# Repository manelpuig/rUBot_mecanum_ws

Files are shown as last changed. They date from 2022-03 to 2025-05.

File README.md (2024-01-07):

# rUBot_mecanum
This rubot_mecanum workspace is organized in the following sections:
| Document | Contents |
|---|---|
| 1. rUBot Mecanum Setup  | Install and Setup rUBot_mecanum workspace|
| 2. rUBot Mecanum Bringup  | Bringup the rUBot_mecanum|
| 3. rUBot Mecanum Control  | Navigation and control|
| 4. rUBot HW Mecanum Slam&Navigation | Slam and Navigation |
| 5. rUBot  Projects | SW and HW projects |
|

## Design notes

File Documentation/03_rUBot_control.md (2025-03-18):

# **rUBot mecanum control**

The objectives of this chapter are:
- control in virtual environment 
- control with real rUBot

We have created different activities in this section:
- Robot performances
    - Keyboard control
    - Python programming control
- Autonomous control with obstacle avoidance
- Robot Wall follower
- Robot go to pose

The final model represents the real rUBot we will use in the laboratory

The rUBot mecanum robot we will work is represented in the picture:
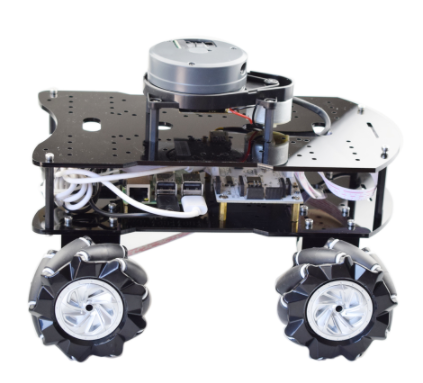
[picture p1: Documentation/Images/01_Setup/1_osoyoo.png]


**Bibliography:**
- https://bitbucket.org/theconstructcore/workspace/projects/PS

## **1. rUBot mecanum performances**

For navigation control of our robot, I have created a ROS Package "rubot_control". If you want to create it from scratch you would have to type:
```shell
cd ~/rubot_mecanum_ws/src
catkin_create_pkg rubot_control rospy std_msgs sensor_msgs geometry_msgs nav_msgs
cd ..
catkin_make
```

### **1.1. Kinematics model of mecanum robot**
The rUBot mecanum is based on a 4-wheels and has a Mecanum-drive kinematics model. We have first to analyse its kinematics model to properly control it.

Wheeled mobile robots may be classified in two major categories, holonomic (omnidirectional) and nonholonomic. 
- **Nonholonomic mobile robots**, such as conventional cars, employ conventional wheels, which prevents cars from moving directly sideways.
- **Holonomic mobile robots**, such as mecanum cars, employ omni or mecanum wheels, which allow lateral and diagonal movements

The rUBot mecanum corresponds to a Kinematic model for Holonomic Mecanum wheeled robot:

Omnidirectional wheeled mobile robots typically employ either omni wheels or mecanum wheels, which are typical wheels augmented with rollers on their outer circumference. These rollers spin freely and they allow sideways sliding while the wheel drives forward or backward without slip in that direction.

The **different movements** our car can perform are:
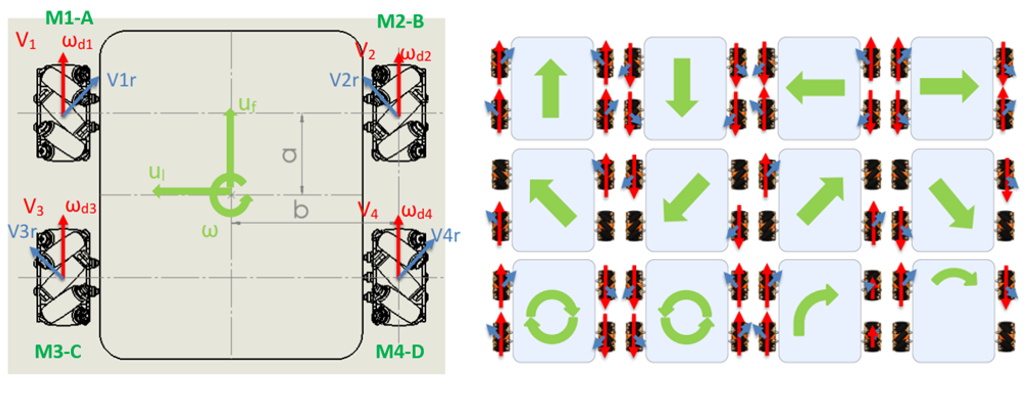
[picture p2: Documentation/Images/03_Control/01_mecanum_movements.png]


The **forces** involved define the robot linear and angular movement:
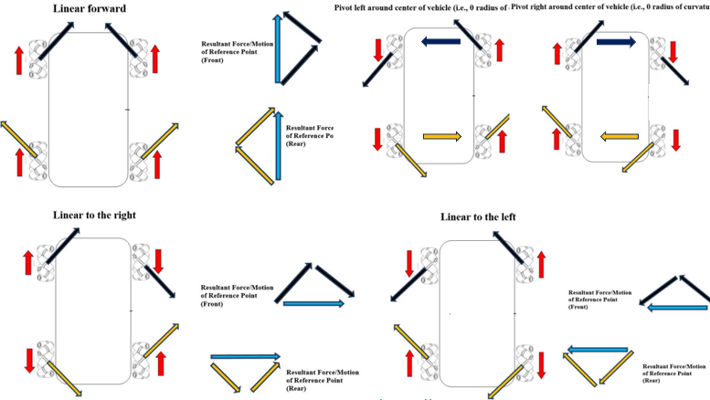
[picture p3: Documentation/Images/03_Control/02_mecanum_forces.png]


The **Forward Kinematics** equations are defined below:


where

- Vi: Linear speed of the wheels.
- ωdi: Angular speed of the wheels.
- Vir: Tangential speed of the rollers.
- ul: Linear velocity of the system on the X axis.
- uf: Linear velocity of the system on the Y axis.
- ω: Speed of rotation of the system on the Z axis.
- a: Distance from the center of the robot to the axis of rotation of the wheel.
- b: Distance from the center of the robot to the center of the width of the wheel.

>(see [Lynch & Park, 2017] for a complete derivation of this model).

In the **Inverse Kinematics** we want to apply a robot movement defined by:
- a linear and angular velocity using a Twist message type published in a /cmd_vel topic. 
- we need to calculate the 4 wheel speeds needed to obtain this robot velocity

This is defined by the following expressions:
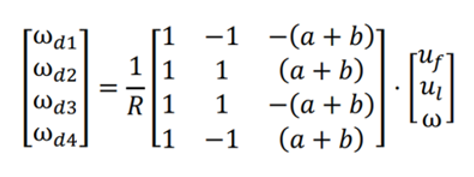
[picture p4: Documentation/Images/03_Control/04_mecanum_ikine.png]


To obtain the **Odometry** we use the information of (uf,ul,w) and Gazebo plugin calculates the POSE of our robot.

The analytical expressions are explained graphically in the picture:
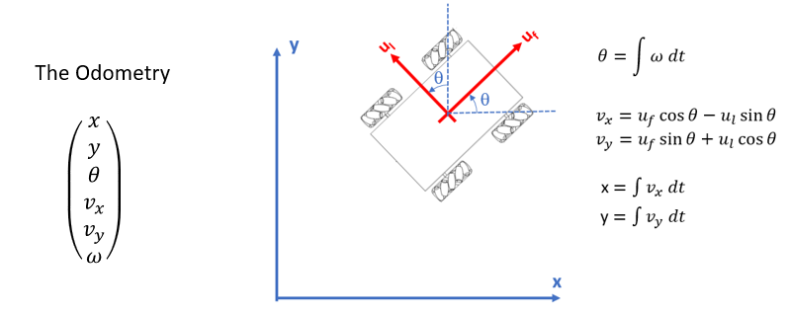
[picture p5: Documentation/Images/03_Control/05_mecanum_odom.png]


In the case of real mecanum robot this is calculated by the robot driver as an arduino program in arduino-mega platform.

### **1.2. rUBot control in VIRTUAL environment**
We can control the movement of our robot using:
- the keyboard or a joypad
- programatically in python creating a "/rubot_nav" node

We are now ready to launch control actions.

We first bringup our robot:
``` shell
roslaunch rubot_mecanum_description rubot_bringup_sw.launch
```
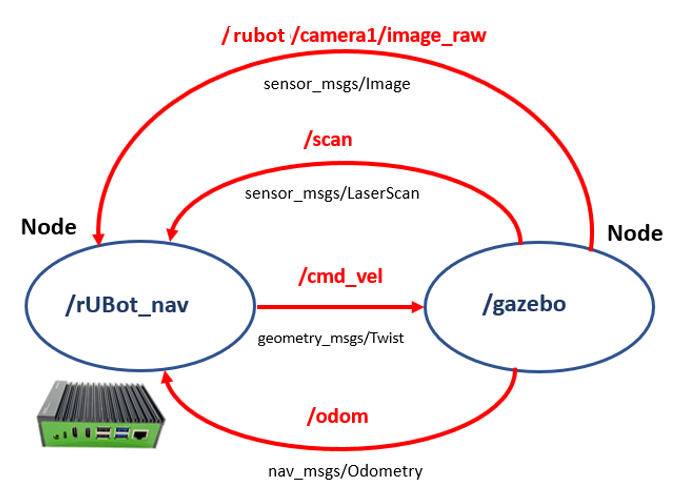
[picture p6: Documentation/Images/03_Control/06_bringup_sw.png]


#### **a) Keyboard control**
You can control the rUBot with the keyboard installing the teleop-twist-keyboard package:
```shell
sudo apt-get install ros-noetic-teleop-twist-keyboard
```

Then you will be able to control the robot with the Keyboard typing:
```shell
rosrun teleop_twist_keyboard teleop_twist_keyboard.py
```
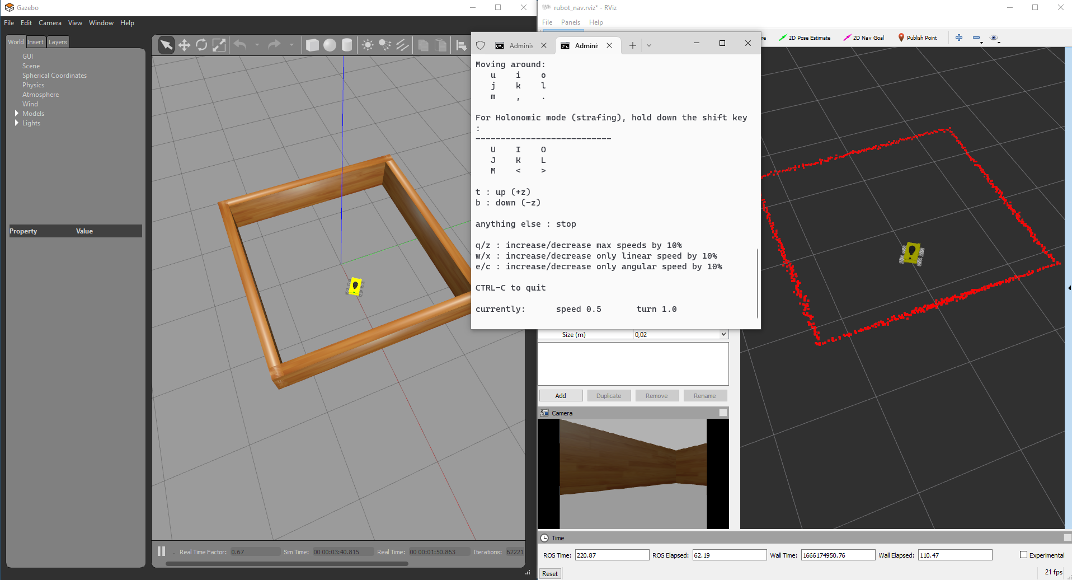
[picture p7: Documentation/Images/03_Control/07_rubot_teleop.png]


#### **b) Python programming control**

A first simple navigation program is created to move the robot according to a speciffic Twist message.

We will create now a first navigation python files in "src" folder:
- rubot_control.py: to define a rubot movement with linear and angular speed during a time td

Specific launch file have been created to launch the node and python file created above:
```shell
roslaunch rubot_control rubot_control.launch
```
Verify first that the code is working in the simulated environment.

**Activity: rUBot control in a predefined Trajectory**

If the robot moves in the correct direction, you can follow with the next objective: Create a new node for **path trajectory** definition:

- Write a new rubot_path_control.py python file that:
    - creates a rubot_nav node
    - includes parameters: v, w, and trajectory time
    - verify the functions: square_path() and triangular_path()
    - define your proper function (star(), rombe(), etc.)
- Write the corresponding rubot_path_control.launch file
- Verify and demonstrate the execution:
``` shell
roslaunch rubot_control rubot_path_control.launch
```

### **1.3. rUBot control in REAL environment**

In real environment, the bringup process depends on the real robot.

To bringup the rUBot_mecanum, execute in a first terminal:
``` shell
roslaunch rubot_mecanum_description rubot_bringup_hw_arduino.launch
```
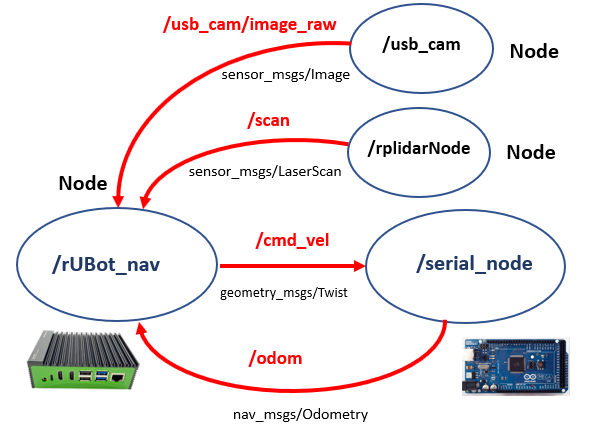
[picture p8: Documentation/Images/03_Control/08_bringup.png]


**Important!**: If you are using the RRL service from TheConstruct, the bringup is already done on boot! You have only to connect to the Real Robot.

#### **a) Keyboard control**
You can control the rUBot with the keyboard if you have first connected to the real robot within RRL service.

#### **b) Joy control**

You can control the rUBot with the Joypad following the instructions in: 
https://dev.to/admantium/radu-control-the-robot-using-a-joystick-976

- 
- In order to work with any gamepad, we need to install additional ROS packages:
```shell
sudo apt-get install ros-noetic-teleop-twist-joy ros-noetic-joy
```
- These packages provide several ways to interact with a connected joypad. To get started, we will run a ROS node called joy_node with the parameter of the detected device file.
```shell
rosrun joy joy_node dev:=/dev/input/js0
```
- to translate the messages from the /joy topic to TWIST messages, another ROS package already performs this translation. We just need to start the teleop_twist_joynode:
```shell
rosrun teleop_twist_joy teleop_node 
```
- connect the gamepad and select the Mode2 (green and red leds)
- Subscribe to the topic /cmd_vel. Then, on your gamepad, identify the deadman switch button (in our gamepad is the triangle button) and you should see messages published on /cmd_vel topic.
- You can see that this enable a non-holonomic movement
- To enable the **holonomic movement**, you have to configure the proper parameters. 
- An exemple is created to start the 2 nodes with the proper configuration parameters. This is the **rubot_joy.launch** file.

```shell
roslaunch rubot_control rubot_joy.launch
```
> For button mapping documentation refer to: http://wiki.ros.org/joy or http://wiki.ros.org/ps3joy
> for detailed configuration of launch file refer to: https://github.com/ros-teleop/teleop_twist_joy/blob/indigo-devel/launch/teleop.launch

Cool! If you have made the bringup of your robot, you will automatically feed these messages to your robot, and you can start moving around, controlled with a gamepad.

#### **c) Smart-Phone control**
ROS-Mobile is an Android application designed for dynamic control and visualization of mobile robotic system operated by the Robot Operating System (ROS). The application uses ROS nodes initializing publisher and subscriber with standard ROS messages. (https://github.com/ROS-Mobile/ROS-Mobile-Android)

- Download from Google Playstore:
Simply go to the Google Playstore Website of the ROS-Mobile app and download it. It will be installed automatically. This video shows the installation and operation process: https://www.youtube.com/watch?v=T0HrEcO-0x0
- Connect via ssh to the Master located in the RaspberryPi4 onboard computer
- Create a proper Dashboard with the joypad desried configuration

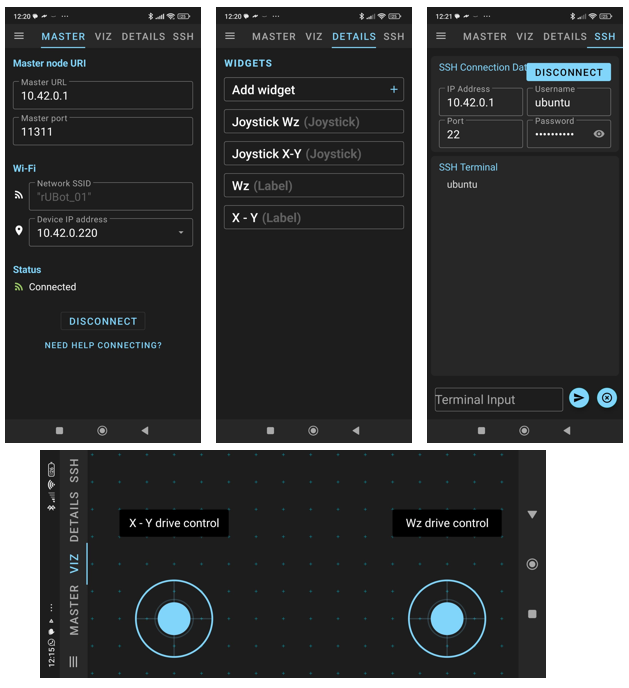
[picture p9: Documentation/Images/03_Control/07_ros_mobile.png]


> Every change you make you have to disconnect and connect again to proper operation

#### **d) Python programming control**
In the previous session we have created a python node to publish a Twist message in /cmd_vel topic. Verify the previous rubot_nav.launch file created for this purpose:
``` shell
roslaunch rubot_control rubot_control.launch
```
**Lab session: rUBot navigation in a predefined Trajectory**

If the robot moves in the correct direction, you can follow with the next objective: Create a new node for **path trajectory** definition:

- Write a new rubot_path_nav.py python file that:
    - creates a rubot_nav node
    - includes parameters: v, w, and trajectory time
    - verify the functions: square_path() and triangular_path()
    - define your proper function (star(), rombe(), etc.
- Write the corresponding rubot_path_nav.launch file
- Verify and demonstrate the execution:
``` shell
roslaunch rubot_control rubot_path_control.launch
```
Verify different trajectories inside your world
Upload the:

- rubot_path_control.launch and rubot_path_control.py files
- Video of the execution in REAL environment

## **2. Autonomous navigation with obstacle avoidance**
We will use now the created world to test the autonomous navigation with obstacle avoidance performance. 

An interesting program is described in: https://www.youtube.com/watch?v=qO7Y1PCkB8g&t=624s

The algorithm description functionality, created in "rubot_self_control.py" file,is:
- The created node makes the robot go forward.
    - LIDAR is allways searching the closest distance and the angle
    - when this distance is lower than a threshold, the robot goes backward with angular speed in the oposite direction of the minimum distance angle.

Let's verify first this behaviour in virtual environment

### **2.1. Self-control in VIRTUAL environment**

We have to launch the "rubot_self_control.launch" file in the "rubot_control" package.
```shell
roslaunch rubot_mecanum_description rubot_bringup_sw.launch
roslaunch rubot_control rubot_self_control.launch
```

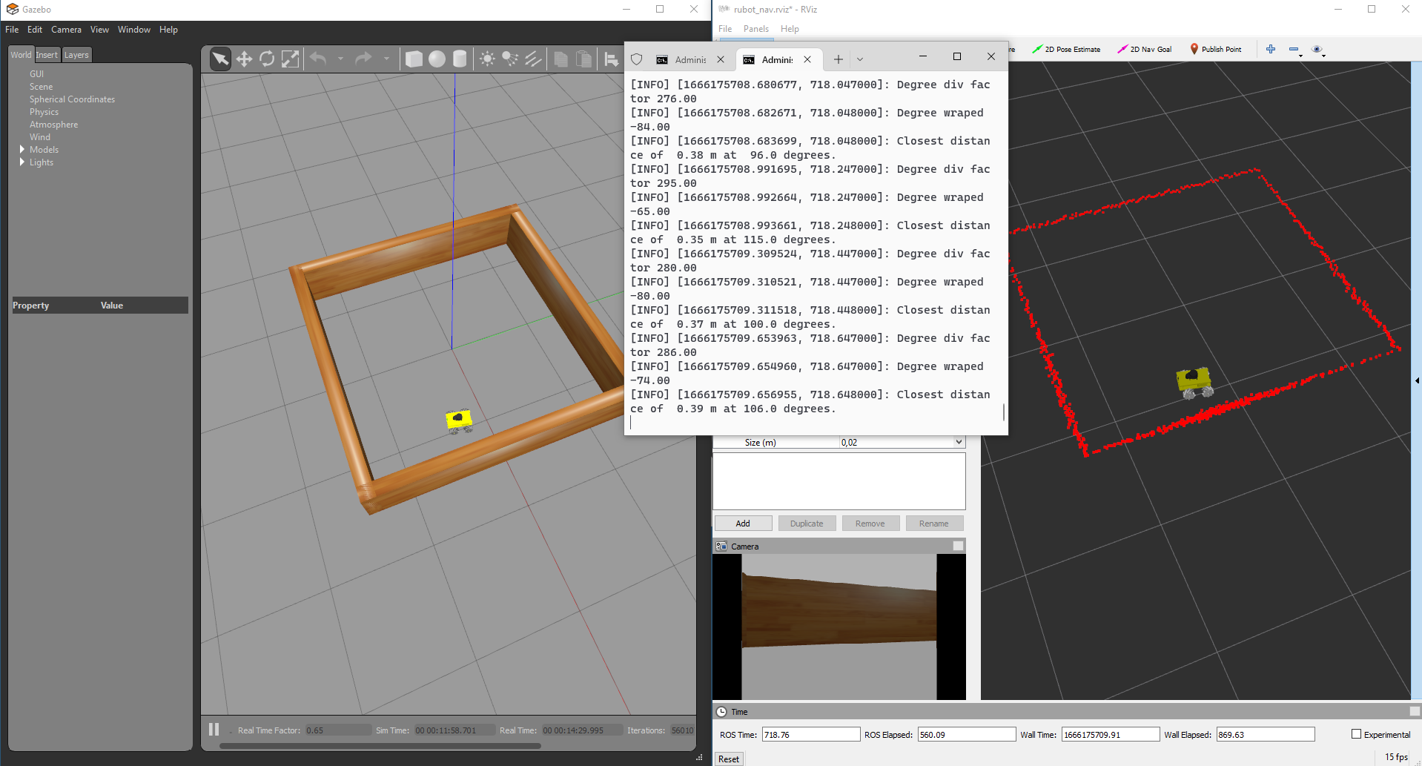
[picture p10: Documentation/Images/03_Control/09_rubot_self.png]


>- Verify in rviz if you have to change the fixed frame to "odom" frame
>- You can test the behaviour when tunning the parameters defined

**Activity: rUBot self-control**

The objective of this activity is to modify the code to move the robot in Holonomic way, for exemple:
-  When the minimum distance is in the right side move the robot over the left side

Design the code using the Holonomic robot performances, and upload:
- the file "rubot_self_control_holonomic.py"
- a video of the current behaviour in your designed world

### **2.2. Self-control control in REAL environment**

Connect first to the Real robot within RRL service.

Then verify the obstacle avoidance behaviour for different parameter values.
```shell
roslaunch rubot_control rubot_self_control.launch
```
The robot is not working as expected because the number of laser beams is not 720 as in simulation!

**Lab Activity: rUBot self-control**

The objective of this lab session is:
- take into account the number of laser beams of your Lidar in the python code
- verify the designed holonomic self-control node you have created for virtual environment in the previous activity.

Upload the:
- rubot_self_control_holonomic.launch and rubot_self_control_holonomic.py files
- Video of the execution in REAL environment

## **3. Wall Follower**
Follow the wall accuratelly is an interesting challenge to make a map with precision to apply SLAM techniques for navigation purposes.

There are 2 main tasks:
- Create a python file "rubot_wall_follower.py" to perform the wall follower in the maze of our mecanum robot
- Create a launch file "rubot_wall_follower.launch" to initialyse all the needed nodes in our system for this control task

### **3.1. Wall follower in VIRTUAL environment**

We have created a rubot_wall_follower_rg.py file based on the reading distances from LIDAR in the ranges: front, front-right, right and back-right, and perform a specific actuation in function of the minimum distance readings.

Follow the instructions to create the rubot_wall_follower_rg.py python file: https://www.theconstructsim.com/wall-follower-algorithm/

The algorith is based on laser ranges test and depends on the LIDAR type:
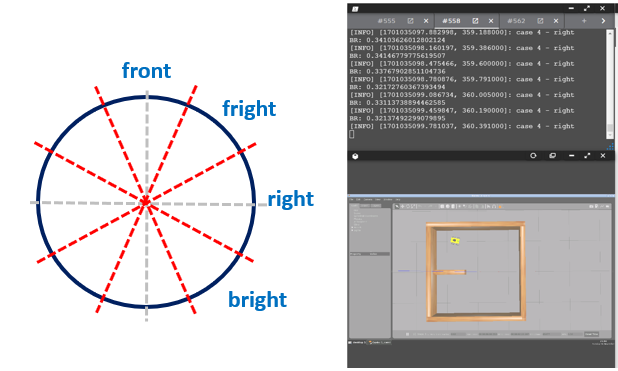
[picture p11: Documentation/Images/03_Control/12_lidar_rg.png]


Open a terminal and type:
```shell
roslaunch rubot_mecanum_description rubot_bringup_sw.launch
roslaunch rubot_control rubot_wall_follower_rg.launch
```
The wall-follower algorithm is not finished and surelly your robot is not able to follow the wall!

**Activity: rUBot wall-follower**

The objective of this activity is:
- Understand the wall-follower algorithm
- complete the code to follow the walls of your designed world
- verify the performances with a concave corners
- create a new algorithm using the holonomic performances of rUBot mecanum

Upload:
- the rubot_wall_follower.py code completed
- video of simulated behaviour in concave corners
- the proposed code "rubot_wall_follower_holonomic.py"
- video of simulated behaviour with holonomic performances

### **3.2. Wall follower in REAL environment**

Connect first to the Real robot within RRL service.

Then verify the obstacle avoidance behaviour for different created programs.

```shell
roslaunch rubot_control rubot_wall_follower_rg.launch
```
**Lab Activity 5: rUBot wall-follower HW**

The objective of this activity is:
- verify the performances of the designed code in the previous activity with your real rUBot
- Improve your new algorithm using the holonomic performances of rUBot mecanum

Upload:
- video of simulated behaviour in concave corners
- the proposed code "rubot_wall_follower_holonomic.py"

## **4. Go to POSE**
Define a specific Position and Orientation as a target point to go:
- x target point
- y target point
- f yaw orientation angle in deg

### **4.1. Go to POSE in VIRTUAL environment**

A node is created in "rubot_go2pose.py" file to reach the POSE destination with a tolerance. We have modified the python script developed in turlesim control package according to the odom message type

For validation type:
```shell
roslaunch rubot_mecanum_description rubot_bringup_sw.launch
roslaunch rubot_control rubot_go2pose.launch
```
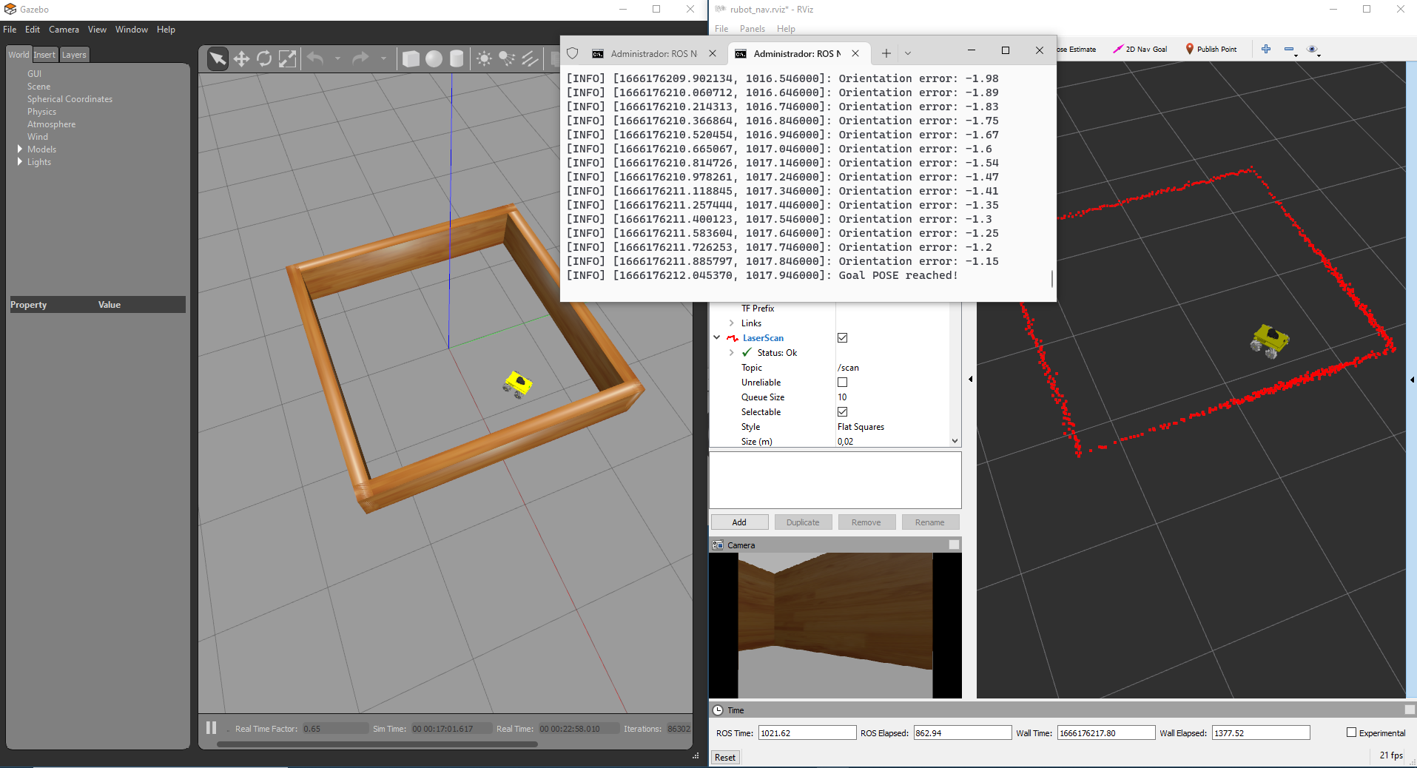
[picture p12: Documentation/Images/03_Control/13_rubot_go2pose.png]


Test different POSE targets before to test it with REAL robot.

### **4.2. Go to POSE in REAL environment**

In a real environment, there is very important the POSE precision. The Odometry computing is made with wheels readings. The floor characteristics and slings can produce inacuracies in odometry calculations.

It is important the include other sensors to obtain a better accuracy. In our case we have included an IMU sensor to obtain a better measurement of the orientation.

We will test the obtained POSE accuracy computing the Odometry with the wheel readigns

Connect first to the Real robot within RRL service.

- Then verify the same node with the real Mecanum robot:
```shell
roslaunch rubot_mecanum_description rubot_go2pose.launch
```

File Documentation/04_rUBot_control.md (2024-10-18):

# **rUBot mecanum control**

The objectives of this chapter are:
- control in virtual environment 
- control with real rUBot

We have created different activities in this section:
- Robot performances
    - Keyboard control
    - Python programming control
- Autonomous control with obstacle avoidance
- Robot Wall follower
- Robot go to pose

The final model represents the real rUBot we will use in the laboratory

The rUBot mecanum robot we will work is represented in the picture:


**Bibliography:**
- https://bitbucket.org/theconstructcore/workspace/projects/PS

## **1. rUBot mecanum performances**

For navigation control of our robot, I have created a ROS Package "rubot_control". If you want to create it from scratch you would have to type:
```shell
cd ~/rubot_mecanum_ws/src
catkin_create_pkg rubot_control rospy std_msgs sensor_msgs geometry_msgs nav_msgs
cd ..
catkin_make
```

### **1.1. Kinematics model of mecanum robot**
The rUBot mecanum is based on a 4-wheels and has a Mecanum-drive kinematics model. We have first to analyse its kinematics model to properly control it.

Wheeled mobile robots may be classified in two major categories, holonomic (omnidirectional) and nonholonomic. 
- **Nonholonomic mobile robots**, such as conventional cars, employ conventional wheels, which prevents cars from moving directly sideways.
- **Holonomic mobile robots**, such as mecanum cars, employ omni or mecanum wheels, which allow lateral and diagonal movements

The rUBot mecanum corresponds to a Kinematic model for Holonomic Mecanum wheeled robot:

Omnidirectional wheeled mobile robots typically employ either omni wheels or mecanum wheels, which are typical wheels augmented with rollers on their outer circumference. These rollers spin freely and they allow sideways sliding while the wheel drives forward or backward without slip in that direction.

The **different movements** our car can perform are:


The **forces** involved define the robot linear and angular movement:


The **Forward Kinematics** equations are defined below:


where

- Vi: Linear speed of the wheels.
- ωdi: Angular speed of the wheels.
- Vir: Tangential speed of the rollers.
- ul: Linear velocity of the system on the X axis.
- uf: Linear velocity of the system on the Y axis.
- ω: Speed of rotation of the system on the Z axis.
- a: Distance from the center of the robot to the axis of rotation of the wheel.
- b: Distance from the center of the robot to the center of the width of the wheel.

>(see [Lynch & Park, 2017] for a complete derivation of this model).

In the **Inverse Kinematics** we want to apply a robot movement defined by:
- a linear and angular velocity using a Twist message type published in a /cmd_vel topic. 
- we need to calculate the 4 wheel speeds needed to obtain this robot velocity

This is defined by the following expressions:


To obtain the **Odometry** we use the information of (uf,ul,w) and Gazebo plugin calculates the POSE of our robot.

The analytical expressions are explained graphically in the picture:


In the case of real mecanum robot this is calculated by the robot driver as an arduino program in arduino-mega platform.

### **1.2. rUBot control in VIRTUAL environment**
We can control the movement of our robot using:
- the keyboard or a joypad
- programatically in python creating a "/rubot_nav" node

We are now ready to launch control actions.

We first bringup our robot:
``` shell
roslaunch rubot_mecanum_description rubot_bringup_sw_custom.launch
```


#### **a) Keyboard control**
You can control the rUBot with the keyboard installing the following packages:
```shell
sudo apt-get install ros-noetic-teleop-tools
sudo apt-get install ros-noetic-teleop-twist-keyboard
```

Then you will be able to control the robot with the Keyboard typing:
```shell
rosrun key_teleop key_teleop.py /key_vel:=/cmd_vel
or
rosrun teleop_twist_keyboard teleop_twist_keyboard.py
```


#### **b) Python programming control**

A first simple navigation program is created to move the robot according to a speciffic Twist message.

We will create now a first navigation python files in "src" folder:
- rubot_control.py: to define a rubot movement with linear and angular speed during a time td

Specific launch file have been created to launch the node and python file created above:
```shell
roslaunch rubot_control rubot_control.launch
```
Verify first that the code is working in the simulated environment.

**Activity 4: rUBot control in a predefined Trajectory**

If the robot moves in the correct direction, you can follow with the next objective: Create a new node for **path trajectory** definition:

- Write a new rubot_path_control.py python file that:
    - creates a rubot_nav node
    - includes parameters: v, w, and trajectory time
    - verify the functions: square_path() and triangular_path()
    - define your proper function (star(), rombe(), etc.)
- Write the corresponding rubot_path_control.launch file
- Verify and demonstrate the execution:
``` shell
roslaunch rubot_control rubot_path_control.launch
```

### **1.3. rUBot control in REAL environment**

In real environment, the bringup process depends on the real robot.

To bringup the rUBot_mecanum, execute in a first terminal:
``` shell
roslaunch rubot_mecanum_description rubot_bringup_hw_arduino.launch
```


#### **a) Keyboard control**
You can control the rUBot with the keyboard installing the following packages:
```shell
sudo apt-get install ros-noetic-teleop-tools
sudo apt-get install ros-noetic-teleop-twist-keyboard
```

Then you will be able to control the robot with the Keyboard typing:
```shell
rosrun key_teleop key_teleop.py /key_vel:=/cmd_vel
or
rosrun teleop_twist_keyboard teleop_twist_keyboard.py
```

#### **b) Joy control**
You can control the rUBot with the Joypad following the instructions in: 
https://dev.to/admantium/radu-control-the-robot-using-a-joystick-976

- In order to work with any gamepad, we need to install additional ROS packages:
```shell
sudo apt-get install ros-noetic-teleop-twist-joy ros-noetic-joy
```
- These packages provide several ways to interact with a connected joypad. To get started, we will run a ROS node called joy_node with the parameter of the detected device file.
```shell
rosrun joy joy_node dev:=/dev/input/js0
```
- to translate the messages from the /joy topic to TWIST messages, another ROS package already performs this translation. We just need to start the teleop_twist_joynode:
```shell
rosrun teleop_twist_joy teleop_node 
```
- connect the gamepad and select the Mode2 (green and red leds)
- Subscribe to the topic /cmd_vel. Then, on your gamepad, identify the deadman switch button (in our gamepad is the triangle button) and you should see messages published on /cmd_vel topic.
- You can see that this enable a non-holonomic movement
- To enable the **holonomic movement**, you have to configure the proper parameters. 
- An exemple is created to start the 2 nodes with the proper configuration parameters. This is the **rubot_joy.launch** file.

```shell
roslaunch rubot_control rubot_joy.launch
```
> For button mapping documentation refer to: http://wiki.ros.org/joy or http://wiki.ros.org/ps3joy
> for detailed configuration of launch file refer to: https://github.com/ros-teleop/teleop_twist_joy/blob/indigo-devel/launch/teleop.launch

Cool! If you have made the bringup of your robot, you will automatically feed these messages to your robot, and you can start moving around, controlled with a gamepad.

#### **c) Smart-Phone control**
ROS-Mobile is an Android application designed for dynamic control and visualization of mobile robotic system operated by the Robot Operating System (ROS). The application uses ROS nodes initializing publisher and subscriber with standard ROS messages. (https://github.com/ROS-Mobile/ROS-Mobile-Android)

- Download from Google Playstore:
Simply go to the Google Playstore Website of the ROS-Mobile app and download it. It will be installed automatically. This video shows the installation and operation process: https://www.youtube.com/watch?v=T0HrEcO-0x0
- Connect via ssh to the Master located in the RaspberryPi4 onboard computer
- Create a proper Dashboard with the joypad desried configuration



> Every change you make you have to disconnect and connect again to proper operation

#### **d) Python programming control**
In the previous session we have created a python node to publish a Twist message in /cmd_vel topic. Verify the previous rubot_nav.launch file created for this purpose:
``` shell
roslaunch rubot_control rubot_control.launch
```
**Lab Activity 3: rUBot navigation in a predefined Trajectory**

If the robot moves in the correct direction, you can follow with the next objective: Create a new node for **path trajectory** definition:

- Write a new rubot_path_nav.py python file that:
    - creates a rubot_nav node
    - includes parameters: v, w, and trajectory time
    - verify the functions: square_path() and triangular_path()
    - define your proper function (star(), rombe(), etc.
- Write the corresponding rubot_path_nav.launch file
- Verify and demonstrate the execution:
``` shell
roslaunch rubot_control rubot_path_control.launch
```
Verify different trajectories inside your world
Upload the:

- rubot_path_control.launch and rubot_path_control.py files
- Video of the execution in REAL environment

## **2. Autonomous navigation with obstacle avoidance**
We will use now the created world to test the autonomous navigation with obstacle avoidance performance. 

The algorithm description functionality, created in "rubot_self_control.py" file,is:
- The created node makes the robot go forward.
    - LIDAR is allways searching the closest distance and the angle
    - when this distance is lower than a threshold, the robot goes backward with angular speed in the oposite direction of the minimum distance angle.

Let's verify first this behaviour in virtual environment

### **2.1. Self-control in VIRTUAL environment**

We have to launch the "rubot_self_control.launch" file in the "rubot_control" package.
```shell
roslaunch rubot_mecanum_description rubot_bringup_sw_custom.launch
roslaunch rubot_control rubot_self_control.launch
```



>- Verify in rviz if you have to change the fixed frame to "odom" frame
>- You can test the behaviour when tunning the parameters defined

**Activity: rUBot self-control**

The objective of this activity is to modify the code to move the robot in Holonomic way, for exemple:
-  When the minimum distance is in the right side move the robot over the left side

Design the code using the Holonomic robot performances, and upload:
- the file "rubot_self_control_holonomic.py"
- a video of the current behaviour in your designed world

### **2.2. Self-control control in REAL environment**

To bringup the rUBot mecanum robot, execute:
```shell
roslaunch rubot_mecanum_description rubot_bringup_hw_arduino.launch
```
Then verify the obstacle avoidance behaviour for different parameter values.
```shell
roslaunch rubot_control rubot_self_control.launch
```
The robot is not working as expected because the number of laser beams is nor 720 as in simulation!

**Lab Activity: rUBot self-control**

The objective of this lab session is:
- take into account the number of laser beams of your Lidar in the python code
- verify the designed holonomic self-control node you have created for virtual environment in the previous activity.

Upload the:
- rubot_self_control_holonomic.launch and rubot_self_control_holonomic.py files
- Video of the execution in REAL environment

## **3. Wall Follower**
Follow the wall accuratelly is an interesting challenge to make a map with precision to apply SLAM techniques for navigation purposes.

There are 2 main tasks:
- Create a python file "rubot_wall_follower.py" to perform the wall follower in the maze of our mecanum robot
- Create a launch file "rubot_wall_follower.launch" to initialyse all the needed nodes in our system for this control task

### **3.1. Wall follower in VIRTUAL environment**

We have created a rubot_wall_follower_rg.py file based on the reading distances from LIDAR in the ranges: front, front-right, right and back-right, and perform a specific actuation in function of the minimum distance readings.

Follow the instructions to create the rubot_wall_follower_rg.py python file: https://www.theconstructsim.com/wall-follower-algorithm/

The algorith is based on laser ranges test and depends on the LIDAR type:


Open a terminal and type:
```shell
roslaunch rubot_mecanum_description rubot_bringup_sw_custom.launch
roslaunch rubot_control rubot_wall_follower_rg.launch
```
The wall-follower algorithm is not finished and surelly your robot is not able to follow the wall!

**Activity: rUBot wall-follower**

The objective of this activity is:
- Understand the wall-follower algorithm
- complete the code to follow the walls of your designed world
- verify the performances with a concave corners
- create a new algorithm using the holonomic performances of rUBot mecanum

Upload:
- the rubot_wall_follower.py code completed
- video of simulated behaviour in concave corners
- the proposed code "rubot_wall_follower_holonomic.py"
- video of simulated behaviour with holonomic performances

### **3.2. Wall follower in REAL environment**

To bringup the Mecanum robot, execute in a first terminal:
```shell
roslaunch rubot_mecanum_description rubot_bringup_hw_arduino.launch
```
Then verify the obstacle avoidance behaviour for different created programs.

```shell
roslaunch rubot_control rubot_wall_follower_rg_custom.launch
```
**Lab Activity 5: rUBot wall-follower HW**

The objective of this activity is:
- verify the performances of the designed code in the previous activity with your real rUBot
- Improve your new algorithm using the holonomic performances of rUBot mecanum

Upload:
- video of simulated behaviour in concave corners
- the proposed code "rubot_wall_follower_holonomic.py"

## **4. Go to POSE**
Define a specific Position and Orientation as a target point to go:
- x target point
- y target point
- f yaw orientation angle in deg

### **4.1. Go to POSE in VIRTUAL environment**

A node is created in "rubot_go2pose.py" file to reach the POSE destination with a tolerance. We have modified the python script developed in turlesim control package according to the odom message type

For validation type:
```shell
roslaunch rubot_mecanum_description rubot_bringup_sw_custom.launch
roslaunch rubot_control rubot_go2pose.launch
```


Test different POSE targets before to test it with REAL robot.

### **4.2. Go to POSE in REAL environment**

In a real environment, there is very important the POSE precision. The Odometry computing is made with wheels readings. The floor characteristics and slings can produce inacuracies in odometry calculations.

It is important the include other sensors to obtain a better accuracy. In our case we have included an IMU sensor to obtain a better measurement of the orientation.

We will test the obtained POSE accuracy with:
- Computing the Odometry with the wheel readigns
- Computing the Odometry with the wheel readigns but measuring the robot orientation using the IMU sensor.

We will have to:
- upload a new arduino program to read and calibrate the IMU sensor to measure the robot orientation
- Calibrate the IMU sensor only a first time with speciffic arduino program
- Bringup the Mecanum robot, using a new arduino program to measure the robot orientation with the IMU sensor:
```shell
roslaunch rubot_mecanum_description rubot_bringup_hw_arduino.launch
```
- Then verify the same node with the real Mecanum robot:
```shell
roslaunch rubot_mecanum_description rubot_go2pose.launch
```

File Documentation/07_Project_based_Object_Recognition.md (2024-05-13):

# Project based on Object recognition

We will describe the Computer Vision based method to identify the Traffic Sign

## Using the RbpyCam

```python
#!/usr/bin/env python

import rospy
from sensor_msgs.msg import Image
from cv_bridge import CvBridge, CvBridgeError
import cv2
import numpy as np
```
**Capturing an image from the camera**

We gonna create a class for encapsuling the attributes and callback function:

```python
class TakeAShot(object):

 def __init__(self):
        self.image_sub = rospy.Subscriber("/camera/rgb/image_raw", Image, self.camera_callback)
        self.bridge_object = CvBridge()
```
The callback function will recieve the Image object from the camera in a missage and then it will save the Image as a png file in your 

```python
 def camera_callback(self,data):
      try:
           # We select bgr8 because its the OpenCV encoding by default
           cv_image = self.bridge_object.imgmsg_to_cv2(data, desired_encoding="bgr8")
           cv2.imwrite("image.png", cv_image)
      except CvBridgeError as e:
           print(e)        
```     		
The main is as usual:

```python
def main():

    rospy.init_node('take_a_shot', anonymous=True)
    take_a_shot = TakeAShot()
    try:
        rospy.spin()
    except KeyboardInterrupt:
        print("Shutting down")

if __name__ == '__main__':
    main()
```

### How to send a sequence of goals to ROS NavStack

* [Sending a sequence of Goals to ROS NavStack with Python](https://hotblackrobotics.github.io/en/blog/2018/01/29/seq-goals-py/)

### Basic Tutorials for image analysis using OpenCV
* [Shape Detection Using findContourns and approxPolyDP ](https://www.pyimagesearch.com/2016/02/08/opencv-shape-detection/)
* [Arrow Interpretation using findContourns and approxPolyDP](https://programs.wiki/wiki/use-opencv-to-judge-the-arrow-direction.html)
* [Detecting lines using Canny Edges and Hough Lines](https://docs.opencv.org/3.4/d9/db0/tutorial_hough_lines.html) --> [Example code ](https://github.com/michael-pacheco/opencv-arrow-detection)
* [Color Detection using HSV space](https://www.pyimagesearch.com/2015/09/14/ball-tracking-with-opencv/)
* [HSV color picker (in opencv H value goes from 0 to 179)](https://alloyui.com/examples/color-picker/hsv.html)

### Final Exercise:
#### First scenario: Image processing

* Load the room map 
* Start the navigation stack. 
* Get the coordinates of all the traffic sign using Rviz.
* Write a Python node with the folowing behaviour:
	* Go to the first sign.
	* When the robot stops:
		* take an image. 
		* recognize the object using image processing by coulour and shape. 
		* go to next sign according the signs:
			* Left: go to next sign on the left
			* Right: go to next sign on the right
			* STOP: Shutdown node.
			* Forbidden: continues to the next sign  	 

#### Second scenario: Computer Vision

* Load the room map 
* Start the navigation stack. 
* Get the coordinates of all the traffic sign using Rviz.
* Write a Python node with the folowing behaviour:
	* Go to the first sign.
	* When the robot stops:
		* take an image. 
        * recognize the object using TensorFlow model and do inference on each image
		* go to next sign according the signs:
			* Left: go to next sign on the left
			* Right: go to next sign on the right
			* STOP: Shutdown node.
			* Forbidden: continues to the next sign  

### How to train and use a TensorFlow model for object recognition:
* Go to https://teachablemachine.withgoogle.com/ and create an image project.
* Collect images with your mobile for each sign and upload them to the project.
* Train the model.
* Export the model as a keras .h5 model: 
* Install Keras and TensorFlow in the Robot: 
    ````python
    sudo pip install keras
    sudo pip install tensorflow
    ````
* Create a ROS node that uses the model for inference:
  
```python

from keras.models import load_model  # TensorFlow is required for Keras to work
import cv2  # Install opencv-python
import numpy as np

# Disable scientific notation for clarity
np.set_printoptions(suppress=True)

# Load the model
model = load_model("keras_Model.h5", compile=False)

# Load the labels
class_names = open("labels.txt", "r").readlines()

# CAMERA can be 0 or 1 based on default camera of your computer
camera = cv2.VideoCapture(0)

while True:
    # Grab the webcamera's image.
    ret, image = camera.read()

    # Resize the raw image into (224-height,224-width) pixels
    image = cv2.resize(image, (224, 224), interpolation=cv2.INTER_AREA)

    # Show the image in a window
    cv2.imshow("Webcam Image", image)

    # Make the image a numpy array and reshape it to the models input shape.
    image = np.asarray(image, dtype=np.float32).reshape(1, 224, 224, 3)

    # Normalize the image array
    image = (image / 127.5) - 1

    # Predicts the model
    prediction = model.predict(image)
    index = np.argmax(prediction)
    class_name = class_names[index]
    confidence_score = prediction[0][index]

    # Print prediction and confidence score
    print("Class:", class_name[2:], end="")
    print("Confidence Score:", str(np.round(confidence_score * 100))[:-2], "%")

    # Listen to the keyboard for presses.
    keyboard_input = cv2.waitKey(1)

    # 27 is the ASCII for the esc key on your keyboard.
    if keyboard_input == 27:
        break

camera.release()
cv2.destroyAllWindows()
```

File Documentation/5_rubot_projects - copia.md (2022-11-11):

# **rUBot mecanum challenging projects**

The projects proposed will be based on:
- rUBot navigation using python-based code
- Video and picture caption
- Image processing

The different projects will be:
- 1. rUBot takes photo
- 2. Go to specific point in the map
- 3. Go to specific point in the map and take a photo
- 4. Line follower

The image processing projects will be performed using:
- 2D raspicam
- 3D Inter Realsense camera

References OpenCV:
- http://wiki.ros.org/cv_bridge/Tutorials/ConvertingBetweenROSImagesAndOpenCVImagesPython
- https://docs.opencv.org/4.x/d6/d00/tutorial_py_root.html
- https://github.com/Akshay594/OpenCV/tree/master/tutorials

References InterRealSense:
- https://dev.intelrealsense.com/docs/ros-wrapper
- https://www.youtube.com/watch?v=GhHvuAoFC6I
- https://intel.github.io/robot_devkit_doc/pages/rs_slam.html

References for webcam:
- https://automaticaddison.com/working-with-ros-and-opencv-in-ros-noetic/

References:
- https://learn.turtlebot.com/
- https://learn.turtlebot.com/2015/02/04/1/
- https://learn.turtlebot.com/2015/02/04/2/
- https://learn.turtlebot.com/2015/02/04/3/
- https://github.com/markwsilliman/turtlebot
- http://wiki.ros.org/Camera%2BDynamixelRobotSample/CameraPictureServer
- https://industrial-training-master.readthedocs.io/en/melodic/_source/session5/OpenCV-in-Python.html

The first step is to create a new package "rubot_projects" with dependencies:
- rospy
- sensor_msgs
- std_msgs
- cv_bridge

```shell
catkin_create_pkg rubot_projects rospy std_msgs sensor_msgs cv_bridge
```
This package is already created and ready to use it!. You have not to create it.

We will perform some specific projects related to rUBot vision capabilities in a navigation process.

## **1. rUBot takes photo**
The objective is to program a python code to take a photo using raspicam in gopigo3 robot prototype.

Important information is taken from: https://learn.turtlebot.com/2015/02/04/3/

Follow the procedure:
- Identify the topic name where raspicam publishes the photo as a mesage of type sensor_msgs:
```shell
roslaunch nexus_slam rubot_world.launch 
rostopic list
```
- Then modify the "take_photo.py" python file with:
    - the proper topic name /rubot/camera1/image_raw
    - the proper photo filename in folder path: ./src/rubot_projects/photos/photo_sim.jpg
- run the "take_photo.py" python file to take a photo
```shell
rosrun rubot_projects take_photo.py
```
- Open the "photos" folder and you will see the photo1.jpg created

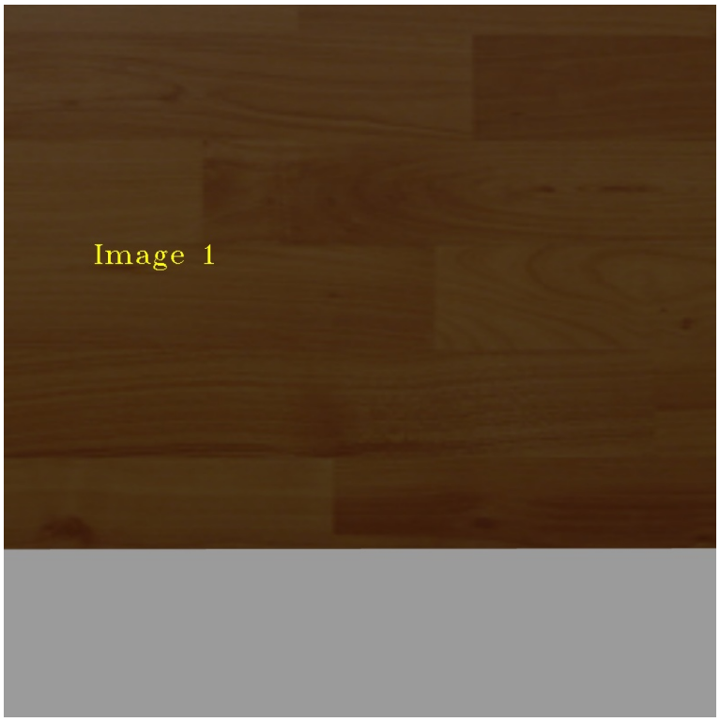
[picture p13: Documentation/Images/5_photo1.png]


## **2. Go to specific point in the map**

In this project we will learn how to send robot a command: “go to a specific position at map”.

The program is extracted from:
- https://github.com/markwsilliman/turtlebot
- https://learn.turtlebot.com/2015/02/03/11/

For this purpose we need to use the **move_base node**. This node:
- subscribes to move_base_simple/goal (geometry_msgs/PoseStamped)
- publishes to cmd_vel (geometry_msgs/Twist)



Follow the procedure:
- Launch Gazebo:
    ```shell
    roslaunch nexus_slam rubot_world.launch
    ```

- Launch the navigation:
    ```shell
    roslaunch nexus_slam rubot_navigation.launch
    ```
- Choose a target point in RVIZ using "Publish point" and select the target coordinates (i.e. x=2.0 y=-0.7)

- open "go_to_specific_point_on_map.py" and specify the target point
    - in line 78 specify the target point, customize the following values so they are appropriate for your location
        - position = {'x': 2.0, 'y' : -0.7}

- Launch the "go_to_specific_point_on_map.py" program:
    ```shell
    rosrun rubot_projects go_to_specific_point_on_map.py
    ```
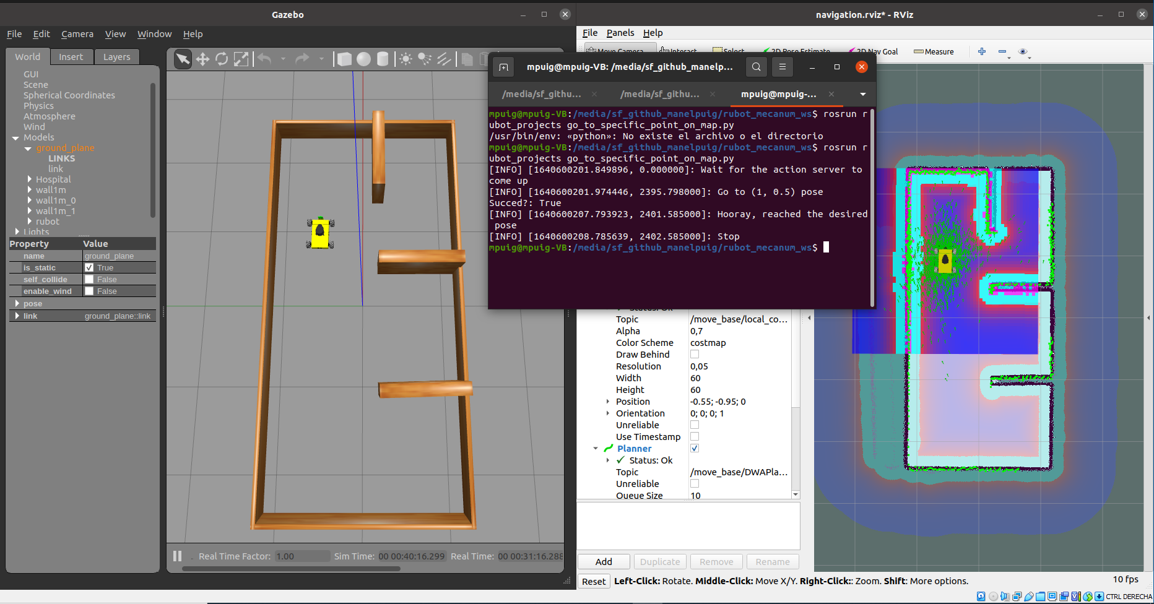
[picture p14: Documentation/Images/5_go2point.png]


## **3. Go to specific point in the map and take a photo**

We will combine our skills from two previous objectives: 
- “Going to a Specific Location on Your Map Using Code” 
- and “Taking a Photo Using Code”. 

The rUBot will go from the start to each goal from the list and take a photo in every position.

We will work with the files from: https://github.com/markwsilliman/turtlebot

Follow the instructions in: https://learn.turtlebot.com/2015/02/04/5/

We use the code go_to_specific_point_on_map.py and take_photo.py from previous exemples. 

We have generated  the python file **"Follow_the_route.py"** that reads input data from "route.yaml" file. 

The YAML file has three lines. It means that there are three goals. Look on the first line:

- {filename: 'photo1.png', position: { x: 0.355, y: -0.2}, quaternion: {r1: 0, r2: 0, r3: -0.628, r4: 0.778}}

    The dumpster.png is the image title for picture. 
    
    The position and quaternion set the goal: the place where rUBot takes a photo. 

The objective is to follow the route and take pictures. 

Proceed with the following steps:

- Launch Gazebo:
    ```shell
    roslaunch nexus_slam rubot_world.launch
    ```

- Run the navigation demo:
    ```shell
    roslaunch nexus_slam rubot_navigation.launch
    ```

- Specify a "route.yaml" file with the points to follow and take photo:

    - {filename: './src/robot_projects/rubot_projects/photos/picture1.png', position: { x: -0.3, y: -0.8}, quaternion: {r1: 0, r2: 0, r3: -0.628, r4: 0.778}}
    - {filename: './src/robot_projects/rubot_projects/photos/picture2.png', position: { x: 1.7, y: -0.7}, quaternion: {r1: 0, r2: 0, r3: 0.936, r4: 0.353}}
    - {filename: './src/robot_projects/rubot_projects/photos/picture3.png', position: { x: 1.7, y: 0.5}, quaternion: {r1: 0, r2: 0, r3: 0.904, r4: -0.427}}

- Open a terminal in the ldestination of pictures and launch the "follow_the_route.py" program:
    ```shell
    rosrun rubot_projects follow_the_route.py
    ```

>Careful!: 
Be sure to execute the rosrun instruction inside the "rubot_mecanum_ws" folder. Review the the absolute path or relative path to the yaml file and the picture path destination.

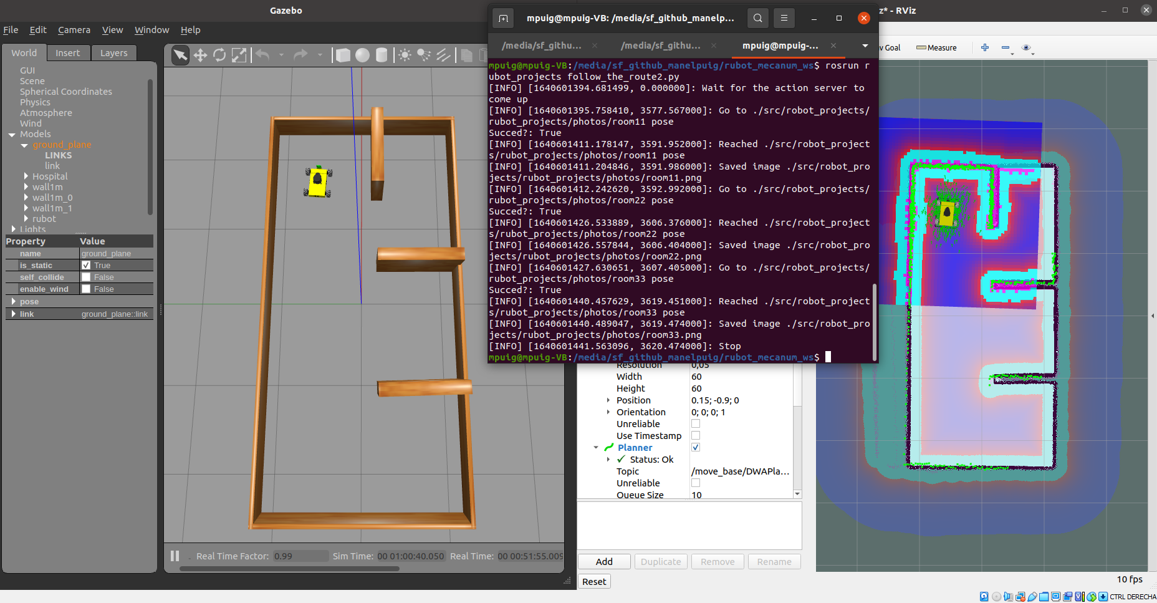
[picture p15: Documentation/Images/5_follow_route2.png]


Improvement!:
- a modified "follow_the_route2.py" and "route2.yaml" is made in order to insert the target orientation in RPY degrees
    - {filename: './src/gopigo3_projects/photos/room11.png', position: { x: -0.3, y: -0.8}, angle: {fi: -90}}
    - {filename: './src/gopigo3_projects/photos/room22.png', position: { x: 1.7, y: -0.7}, angle: {fi: 0}}
    - {filename: './src/gopigo3_projects/photos/room33.png', position: { x: 1.7, y: 0.5}, angle: {fi: 0}}

Launch the "follow_the_route.py" program:

    rosrun rubot_projects follow_the_route2.py 

## **4. Line following**
Detailed official information in: 

- https://www.theconstructsim.com/morpheus-chair-create-a-linefollower-with-rgb-camera-and-ros-episode-5/
- https://www.youtube.com/watch?v=9C7Q8bRERgM
- https://github.com/noshluk2/ROS2-Self-Driving-Car-AI-using-OpenCV

Related to the links:
- http://www.rosject.io/l/8292943/
- https://en.wikipedia.org/wiki/Differential_wheeled_robot

And with the code:
- https://bitbucket.org/theconstructcore/morpheus_chair/src/master/

The nexts steps will be:
- Define a proper simulated world in Gazebo
- spawn the robot model in Gazebo world
- setup the robot with camera
- start the line follower node

### **4.1. world setup**

We have created different models to include in gazebo world:
- Trafic signs
- lights
- road

We will construct first these models in a specific folder:
- .../rubot_mecanum_ws/src/rubot_mecanum_description/models

We have to add this folder to GAZEBO_MODEL_PATH tenvironment variable. This is done either:
-  When using ROS in UBUNTU: in ~/.bashrc file adding this line:
```xml
export GAZEBO_MODEL_PATH=$HOME/Escritorio/rUBot_mecanum_ws/src/rubot_mecanum_description/models:$GAZEBO_MODEL_PATH
```
> If you want to delete any model path from gazebo, load the "gui.ini" file from .gazebo folder. There is a list of model paths and you can delete the one you do not want
- When using ROS in WINDOWS, add in Terminal "command line":
```xml
&& set GAZEBO_MODEL_PATH=C:\Usuarios\puigm\Escritorio\ROS_github\rUBot_mecanum_ws\src\rubot_mecanum_description\models
```
- or copy the models folder in ~/.gazebo/models/
- or you have this folder already in your Gazebo Path if you have created a model using "Building Editor"

#### **a) Traffic sign**
Let's create a "sign board 30" model:
- Open Gazebo as superuser (sudo gazebo)
- select edit --> Model Editor 
- add the meshes (obj files or standard objects) needed to create the sign model
- adjust the size and place the objects in the correct positions to be assembled
- select joint in gazebo (fixed), define the parent and child links, adjust the relative pose, change the joint name if you want and create the model
- save the model as "sign_stand"
- You will see the folder created for this model with 2 files (model.config and model.sdf)
- in model.sdf you can:
  - reduce the mass of the upper links for inertial stability.
  - change the defauld color (Gazebo/Grey)
  - change the dimensions and pose of different links if necessary
- open gazebo and add the generated model to verify the size and mecanical stability.

This model will be used to create all the other traffic signs, for exemple the turn traffic sign:
- Make a copy of this folder with the name "sign_left_turn"
- in model.config file change the name to "sign_left_turn"
- add materials and meshes folders inside "sign_left_turn"
- In materials folder add scripts and textures folder
- In textures folder add the png file with the sign picture (turn.png)
- in scripts add a sign_left_turn.material file with this contents (specify the turn.png file):
```xml
material sign_left_turn/Diffuse
{
  technique
  {
    pass
    {
      texture_unit
      {
        texture turn.png
        filtering anistropic
        max_anisotropy 16
      }
    }
  }
}
```
- Open the model.sdf and change the material properties of link02 where we want to place the turn left texture. Replace the text:
```xml
        <material>
          <lighting>1</lighting>
          <script>
            <uri>file://media/materials/scripts/gazebo.material</uri>
            <name>Gazebo/White</name>
          </script>
          <shader type='pixel'/>
          <emissive>0 0 0 1</emissive>
        </material>
```
by this text:
```xml
        <material>
          <script>
            <uri>model://sign_left_turn/materials/scripts</uri>
            <uri>model://sign_left_turn/materials/textures</uri>
            <name>sign_left_turn/Diffuse</name>
          </script>
        </material>
```

- you have now the turn traffic sign ready!

#### **b) Road surface**
Let's create road surface to follow the road line:
- Open Gazebo (roslaunch gazebo_ros empty_world.launch) and in Building Editor create a model "road1" using a wall with height 5cm width 10m and length 10m. Save this model in "rUBot_mecanum_ws\src\rubot_mecanum_description\models"
- In Power point, create a picture with the road desired texture (proportional xy size is important).
- Save this picture in pgn ot jpeg format using for exemple "Recorte" from windows
- copy the png file to package folder C:/opt/ros/noetic/x64/share/gazebo-10/media/materials/textures
- open package file "C:/opt/ros/noetic/x64/share/gazebo-10/media/materials/scripts/gazebo.material"
- add this code at the end (with png file name):
```xml
material Gazebo/Road_custom
{
  technique
  {
    pass
    {
      ambient 1.0 1.0 1.0 1.0
      diffuse 1.0 1.0 1.0 1.0
      specular 0.2 0.2 0.2 1.0 12.5

      texture_unit
      {
        texture road_custom_1.png
        filtering trilinear
      }
    }
  }
}
```
- Some models and textures are in "rUBot_mecanum_ws/Documentation/Files/Model_Textures/"
- In the "road1" created model ("rUBot_mecanum_ws\src\rubot_mecanum_description\models\road1"), open "model.sdf"
- Change the material/script lines to:
```xml
<material>
  <script>
    <uri>file://media/materials/scripts/gazebo.material</uri>
    <name>Gazebo/Road_custom</name>
  </script>
```
- Open a gazebo_empty-world and create your road_custom_1.world file using the defined models

#### **c) final world**
To add models in our world add each model in the last part of your world file (here starts with empy.world):

```xml
<sdf version="1.5">
  <world name="default">
    <!-- A global light source -->
    <include>
      <uri>model://sun</uri>
    </include>
    <!-- A ground plane -->
    <include>
      <uri>model://ground_plane</uri>
    </include>
    <!-- A traffic sign -->
    <include>
      <uri>model://sign_left_turn</uri>
      <pose>0 0 0.5 0 0 0</pose>
    </include>
    <!-- Line Test 1 -->
    <include>
        <uri>model://line2</uri>
        <name>line_1</name>
        <pose>0 0 0 0 0 0</pose>
      </include> 
    <!-- Line Test 2 -->
    <include>
        <uri>model://line2</uri>
        <name>line_2</name>
        <pose>1 1.025 0 0 0 1.57</pose>
    </include> 
  </world>
</sdf>
```
Alternativelly you can open gazebo and add the desired models in proper location and save it in world format.
```shell
roslaunch gazebo_ros empty_world.launch
```

We spawn our robot into gazebo world:
```shell
roslaunch rubot_projects rubot_bringup.launch
```
To see the camera image, type:
```shell
rosrun rqt_image_view rqt_image_view
```

Start the node line_following_sim
```shell
roslaunch rubot_projects line_following.launch
```
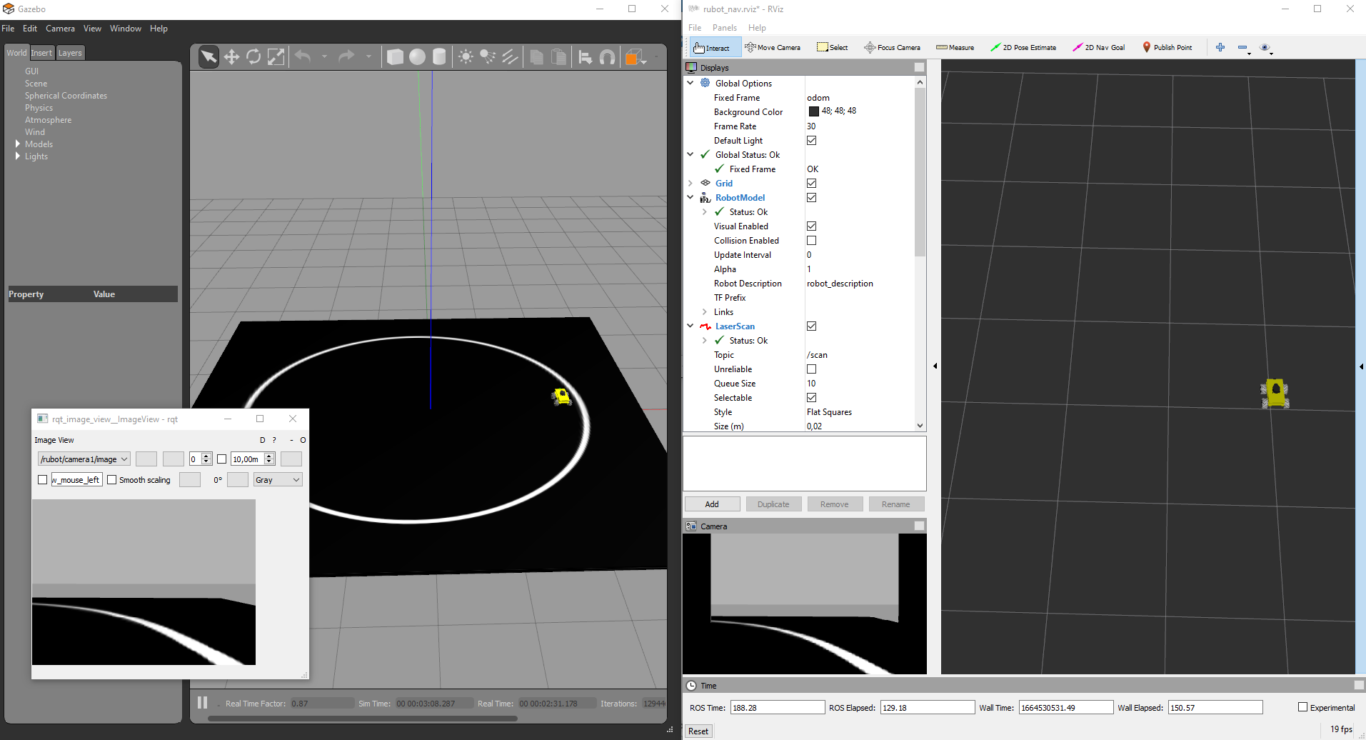
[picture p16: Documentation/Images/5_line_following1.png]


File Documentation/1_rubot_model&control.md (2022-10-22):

# **rUBot mecanum model & control**

Diferent mecanum robot prototypes are available in the market:
- Banggood: https://es.banggood.com/MC100-4WD-Wheeled-Trolley-Smart-Car-Kit-with-Mecanum-Wheel-1-48-Reduction-Ratio-TT-Motor-p-1750584.html?ID=566379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
- OSOYOO: https://www.amazon.es/dp/B082DBYH9G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
- Custom: https://howtomechatronics.com/projects/arduino-mecanum-wheels-robot/
- Nexus: https://www.robotshop.com/es/es/kit-robot-mecanum-4wd-compatible-con-arduino.html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
- Nexus2: https://www.robotshop.com/es/es/kit-robot-arduino-con-rueda-mecanum-4wd-60-mm.html
- Vikep: https://www.amazon.es/VIKEP-AutoPilot-Posicionamiento-automatizado-Conducci%C3%B3n/dp/B09MKFLFKJ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
- VIKEP_Chasis: https://www.amazon.es/VIKEP-Motores-Bricolaje-Mecanum-Plataforma/dp/B09NNFKL3Z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
- KESOTO_Chasis: https://www.amazon.es/KESOTO-Chasis-Coche-Inteligente-Mecanum/dp/B082SQ787K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

The objectives of this chapter are:
- Create a model of our rUBot 
- use rviz package to view the different topics and nodes
- create a model of the virtual environment
- use gazebo package to simulate the robot kinematics and dynamics
- locate the robot in our created environment
- create our firsts programs to control the robot movement with obstacle avoidance

The final model represents the real rUBot we will use in the laboratory

Interesting complementary information could be found:
- https://github.com/RBinsonB/nexus_4wd_mecanum_simulator

The rUBot mecanum robot we will work is represented in the picture:


His main characteristics are: 
- Arduino based control for sensors & actuators
  - Servomotor actuators for the 4 mecanum wheels
  
- RaspberryPi4 High-level onboard control with Ubuntu20 and ROS Noetic
  - RPlidar distance sensor
  - Raspicam 2D camera sensor

**Bibliography:**
- https://bitbucket.org/theconstructcore/workspace/projects/PS

## **1. rUBot mecanum model generation**

First of all, we have to create the "rubot_mecanum_description" package where we will create the rUBot model. In case you want to create it from scratch, type:
```shell
cd ~/Desktop/ROS_github/rubot_mecanum_ws/src
catkin_create_pkg rubot_mecanum_description rospy
cd ..
catkin_make
```
Then open the .bashrc file and verify the environment variables and source to the proper workspace:
```shell
source ~/Desktop/ROS_github/rubot_mecanum_ws/devel/setup.bash
```
> In ROS_windows: add && devel/setup.bat in command line of terminal configuration.

To create our robot model, we use URDF files (Unified Robot Description Format). URDF file is an XML format file for representing a robot model.(http://wiki.ros.org/urdf/Tutorials)

We have created 2 folders for model description:
- URDF: folder where different URDF models are located. In our case rubot_rp.urdf
- meshes: folder where 3D body models in stl format are located. We will have rubot folder.

You can reduce the amount of code in a URDF file using Xacro package. With this package you can use constants, simple math and macros to create your robot model easier and compact.

The main parts of URDF model are:
- links: diferent bodies/plastic elements
- joints: connection between 2 links 
- sensors & actuators plugins (2D camera, LIDAR and DC motors)

The link definition contains:
- visual properties: the origin, geometry and material
- collision properties: the origin and geomnetry
- inertial properties: the origin, mass and inertia matrix

The joint definition contains:
- joint Type (fixed, continuous)
- parent and child frames
- origin frame
- rotation axis

The geometrical definition of our rUBot is:
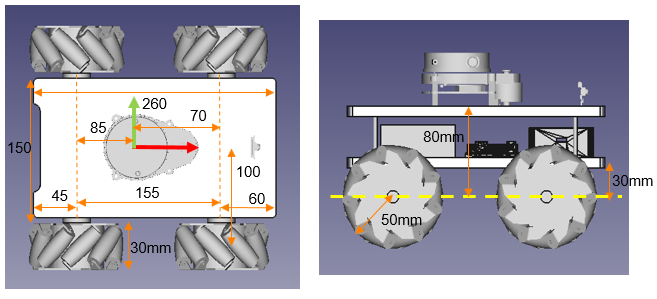
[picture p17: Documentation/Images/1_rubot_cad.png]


In the case or upper left wheel:
```xml
<!-- upper_left_wheel -->
  <joint name="upper_left_wheel_joint" type="continuous">
    <origin rpy="0 0 0" xyz="0.07 0.1 0"/>
    <parent link="base_link"/>
    <child link="upper_left_wheel"/>
    <axis xyz="0 1 0"/>
  </joint>
  <link name="upper_left_wheel">
    <visual>
      <origin rpy="0 0 0" xyz="0 0 0"/>
      <geometry>
        <mesh filename="package://rubot_mecanum_description/meshes/rubot/upper_left_wheel.stl" scale="0.001 0.001 0.001"/>
      </geometry>
      <material name="light_grey"/>
    </visual>
    <collision>
      <origin rpy="-1.57 0 0" xyz="0 0 0"/>
      <geometry>
        <cylinder length="0.03" radius="0.05"/>
      </geometry>
    </collision>
    <inertial>
      <origin rpy="-1.57 0 0" xyz="0.0 0.0 0.0"/>
      <mass value="0.1"/>
      <inertia ixx="0.00007" ixy="0" ixz="0" iyy="0.000125" iyz="0" izz="0.00007"/>
    </inertial>
  </link>
```
> Be careful with base_link:
>
> The inertia matrix can be analytically calculated with the mas and geometry. Be sure the mass is consistent and the inertia Ixx,Iyy and Izz are high enough to avoid underired drift movements. Consider the Inertia matrix you can generate using the **urdf_inertial_calculator.py** program file you have in "Documentation/files/URDF_inertial".
Possible correct values are
  ```xml
      <inertial>
        <origin rpy="0 0 0" xyz="0 0 0"/>
        <mass value="5"/>
        <inertia ixx="6" ixy="0" ixz="0" iyy="6" iyz="0" izz="12"/>
      </inertial>
  ```
The rUBot model includes different sensors and actuators:

Sensors:
- a two-dimensional camera: correspondas to RBPi camera
- a 360º RPLidar A1M8 (https://www.robotshop.com/es/es/rplidar-a1m8-kit-desarrollo-escaner-laser-360-grados.html)

Actuator:
- Mecanum drive actuator: based on 4 DC motors with encoders to obtain the Odometry information

The full model contains also information about the sensor and actuator controllers using specific Gazebo plugins (http://gazebosim.org/tutorials?tut=ros_gzplugins#Tutorial:UsingGazebopluginswithROS). 

Gazebo plugins give your URDF models greater functionality and compatible with ROS messages and service calls for sensor output and motor input. 

These plugins can be referenced through a URDF file, and to insert them in the URDF file, you have to follow the sintax:
### **Camera sensor plugin**
This sensor is integrated as a link and fixed joint for visual purposes. Review the joint and link definition in URDF model.

A driver is needed to view the images.
```xml
  <!-- 2D Camera controller -->
  <gazebo reference="camera">
    <sensor name="camera1" type="camera">
      <update_rate>30.0</update_rate>
      <camera name="front">
        <horizontal_fov>1.3962634</horizontal_fov>
        <image>
          <width>800</width>
          <height>800</height>
          <format>R8G8B8</format>
        </image>
        <clip>
          <near>0.02</near>
          <far>300</far>
        </clip>
      </camera>
      <plugin filename="libgazebo_ros_camera.so" name="camera_controller">
        <alwaysOn>true</alwaysOn>
        <visualize>true</visualize>
        <cameraName>rubot/camera1</cameraName>
        <imageTopicName>image_raw</imageTopicName>
        <cameraInfoTopicName>camera_info</cameraInfoTopicName>
        <frameName>camera</frameName>
        <hackBaseline>0.07</hackBaseline>
        <distortionK1>0.0</distortionK1>
        <distortionK2>0.0</distortionK2>
        <distortionK3>0.0</distortionK3>
        <distortionT1>0.0</distortionT1>
        <distortionT2>0.0</distortionT2>
      </plugin>
    </sensor>
  </gazebo>
  ```
>To view the camera image you can:
> - add the line in the plugin 
> ```xml
><visualize>true</visualize>"
> ```
> -  use rviz
> - type rqt in a terminal and select Plugins->Visualization->Image View
### **LIDAR sensor plugin**
This sensor is integrated as a link and fixed joint for visual purposes. Review the joint and link definition in URDF model.
> Note that rpLIDAR is mounted at 180º and you need to turn the link model and the joint to reflect this in the URDF model.

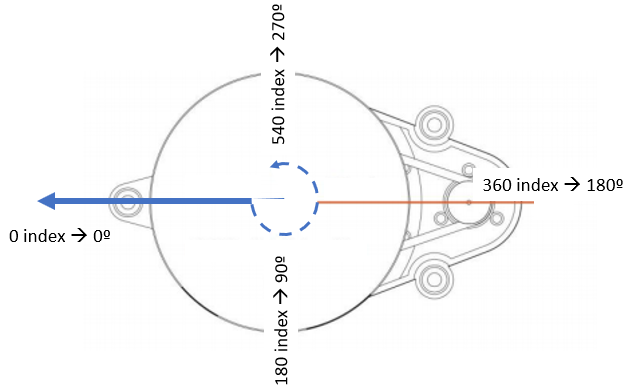
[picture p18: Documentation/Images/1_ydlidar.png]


A driver is needed to see the 720 laser distance points:
```xml
  <!-- Laser Distance Sensor YDLIDAR X4 controller-->
  <gazebo reference="base_scan">
    <sensor name="lds_lfcd_sensor" type="ray">
      <pose>0 0 0 0 0 0</pose>
      <visualize>true</visualize>
      <update_rate>5</update_rate>
      <ray>
        <scan>
          <horizontal>
            <samples>720</samples>
            <resolution>1</resolution>
            <min_angle>0.0</min_angle>
            <max_angle>6.28319</max_angle>
          </horizontal>
        </scan>
        <range>
          <min>0.12</min>
          <max>10</max>
          <resolution>0.015</resolution>
        </range>
        <noise>
          <type>gaussian</type>
          <!-- Noise parameters based on published spec for YDLIDAR X4
              is 1.5% at half range 4m (= 60mm, "+-160mm" accuracy at max. range 8m).
              A mean of 0.0m and stddev of 0.020m will put 99.7% of samples
              within 0.16m of the true reading. -->
          <mean>0.0</mean>
          <stddev>0.02</stddev>
        </noise>
      </ray>
      <plugin filename="libgazebo_ros_laser.so" name="gazebo_ros_lds_lfcd_controller">
        <!-- topicName>/gopigo/scan</topicName -->
        <topicName>scan</topicName>
        <frameName>base_scan</frameName>
      </plugin>
    </sensor>
  </gazebo>
```
>To view the LIDAR rays be sure to add 
> ```xml
><visualize>true</visualize>"
> ```
> or use rviz

It is important to note that:
- the number of points of real RPLidar is usually 720 (one each half degree)
- the number of points of simulated Lidar has to be adapted to the same 720 (by default is 360 (one each degree))
### **Mecanum drive actuator plugin**
A driver is needed to describe the kinematics.This kinematics is described in the "libgazebo_ros_planar_move.so" file and the URDF model will contain the specific gazebo plugin.

This driver is the "Planar Move Plugin" and is described in Gazebo tutorials: http://gazebosim.org/tutorials?tut=ros_gzplugins#AddingaModelPlugin

```xml
  <!-- Mecanum drive controller -->
  <gazebo>
    <plugin name="Mecanum_controller" filename="libgazebo_ros_planar_move.so">
      <commandTopic>cmd_vel</commandTopic>
      <odometryTopic>odom</odometryTopic>
      <odometryFrame>odom</odometryFrame>
      <odometryRate>50.0</odometryRate>
      <robotBaseFrame>base_footprint</robotBaseFrame>
    </plugin>
  </gazebo>
  ```
In this gazebo plugin, the kinematics of the robot configuration is defined:
- Forward kinematics: obtains the robot velocity (linear and angular in /cmd_vel) and POSE (odometry) for speciffic robot wheel speeds
- Inverse kinematics: obtains the robot wheels speeds for a desired robot velocity (linear and angular in /cmd_vel)

We use a specific "display.launch" launch file where we specify the robot model we want to open in rviz with a configuration specified in "urdf.rviz":
```xml
<launch>
  <param name="robot_description" textfile="$(find rubot_mecanum_description)/urdf/rubot.urdf" />
  <node name="joint_state_publisher" pkg="joint_state_publisher" type="joint_state_publisher" />

  <node name="robot_state_publisher" pkg="robot_state_publisher" type="robot_state_publisher" />
  <node name="rviz" pkg="rviz" type="rviz" args="-d $(find rubot_mecanum_description)/rviz/urdf_final.rviz" />
</launch>
```
Launch the ROS visualization tool to check that the model is properly built. 
RViz only represents the robot visual features. You have available all the options to check every aspect of the appearance of the model
```shell
roslaunch rubot_mecanum_description display.launch
```
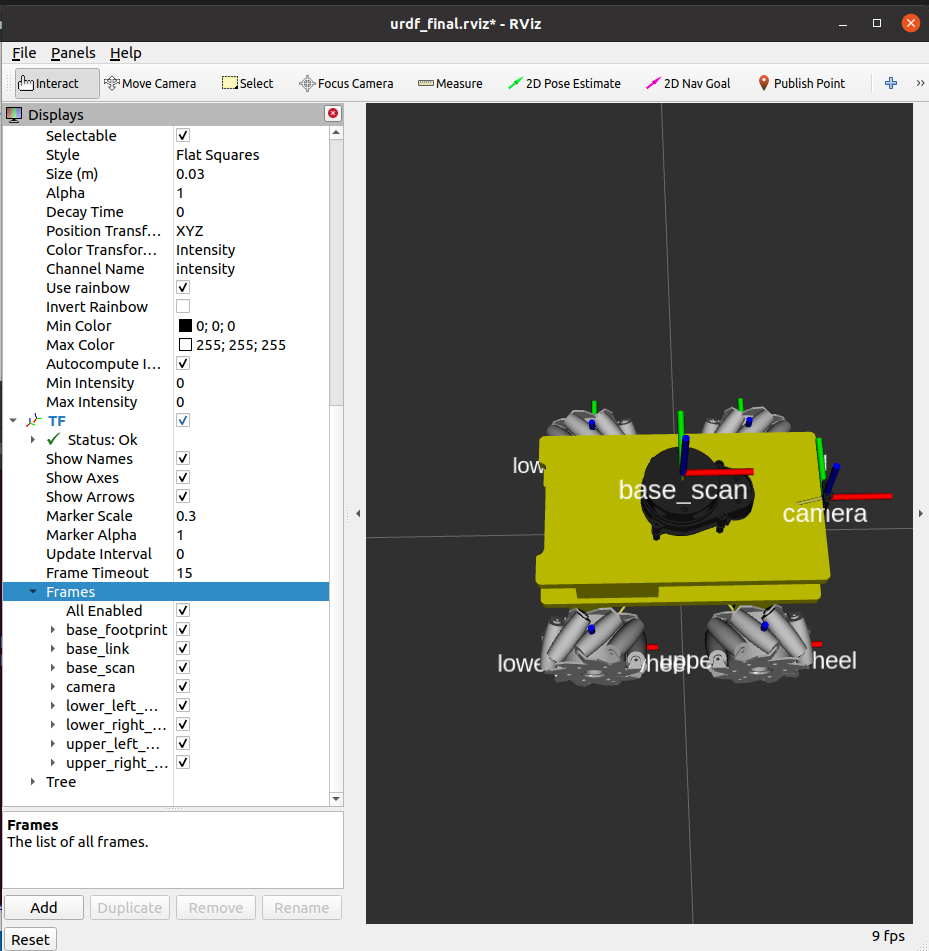
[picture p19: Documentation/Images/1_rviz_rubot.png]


> Colors in rviz: 
>- are defined at the beginning
>- Ensure the "visual" link properties have no "name"
```xml
<robot name="rubot">
  <material name="yellow">
    <color rgba="0.8 0.8 0.0 1.0"/>
  </material>

  ...

    <link name="base_link">
    <visual>
      <origin rpy="0 0 0" xyz="0 0 0"/>
      <geometry>
        <mesh filename="package://rubot_mecanum_description/meshes/rubot/base_link.stl" scale="0.001 0.001 0.001"/>
      </geometry>
      <material name="yellow"/>
    </visual>
```
> Colors in gazebo: 
>- are defined at the end of urdf file:
```xml
<!-- Gazebo colors have to be specified here with predefined Gazebo colors -->
  <gazebo reference="base_link">
    <material>Gazebo/Yellow</material>
  </gazebo>
```

**Activity:**

Design a proper model corresponding to the real rUBot_mecanum you will work with.


You can use FreeCAD to design a custom model and construct manually the URDF file. 

For that it is important to:
- install in VS Code the ROS extension from Microsoft
- Press ctrl+shift+p to access the control commands 
- type ROS and select ROS: Preview URDF
The main steps are:
- Design or obtain the rubot 3D parts. We will deliver the main designed parts (structure, wheels, lidar and camera) and you will have to:
  - contruct the 3D rUBot in freecad ("Documentation/files/Freecad/mainParts")
  - design your own part to be printed and assembled to the rUBot
> Follow the tutorial instructions for FreeCAD in "Documentation/files/Freecad/tutorial".

The final rUBot project design will look like:

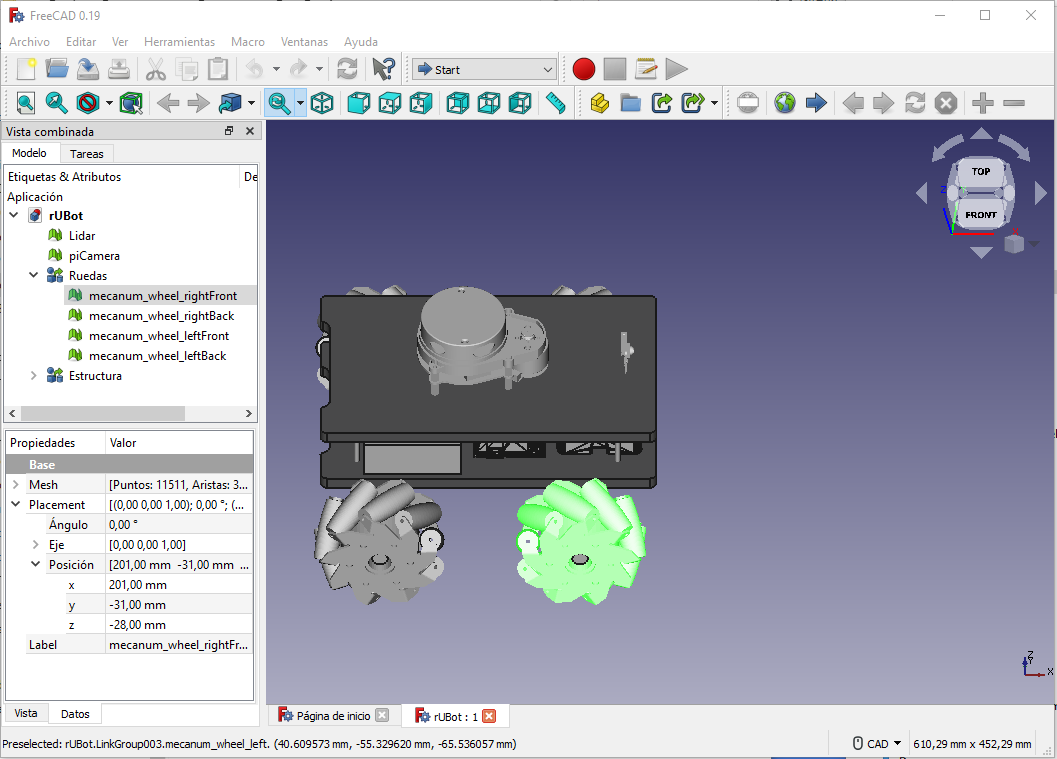
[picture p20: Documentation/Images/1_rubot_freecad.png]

- Create the stl format for your own part and change the origin of part frame in its gravity center. The other parts (base_link, wheels, lidar and picam) are ready. 
- generate the rubot.urdf considering the Vision, Collision and Inertia tags.
  - Vision tag: take into account the position and orientation of each part with respect to the base_link frame. The ROS_URDF preview will help you during the URDF file construction.
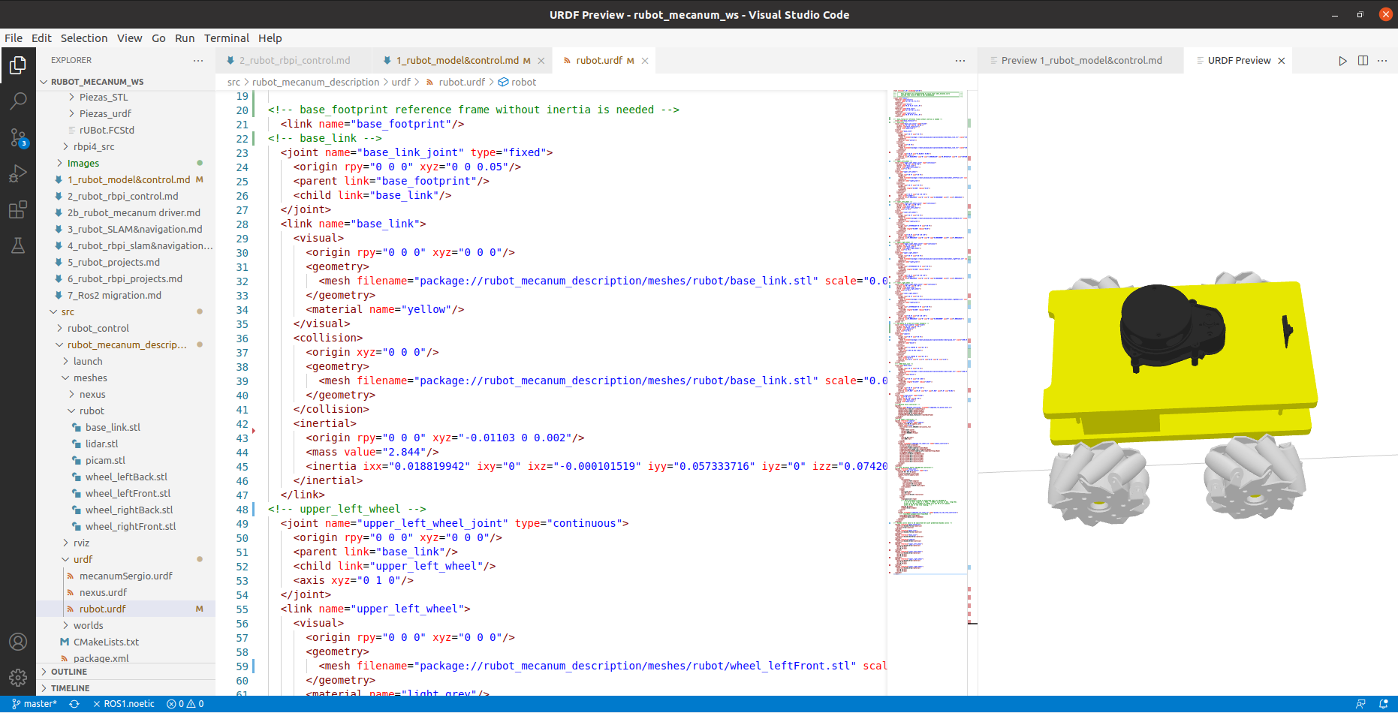
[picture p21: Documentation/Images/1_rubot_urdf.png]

  - Collision tag: consider simple geometrical shapes (box, cylinder and sphere)
  - Inertia tag: consider the Inertia matrix you can generate using the inertia.py program file you have in "Documentation/files/URDF". 

To verify the final frame orientations:
```shell
roslaunch rubot_mecanum_description rubot_world.launch
roslaunch rubot_mecanum_description display.launch
```
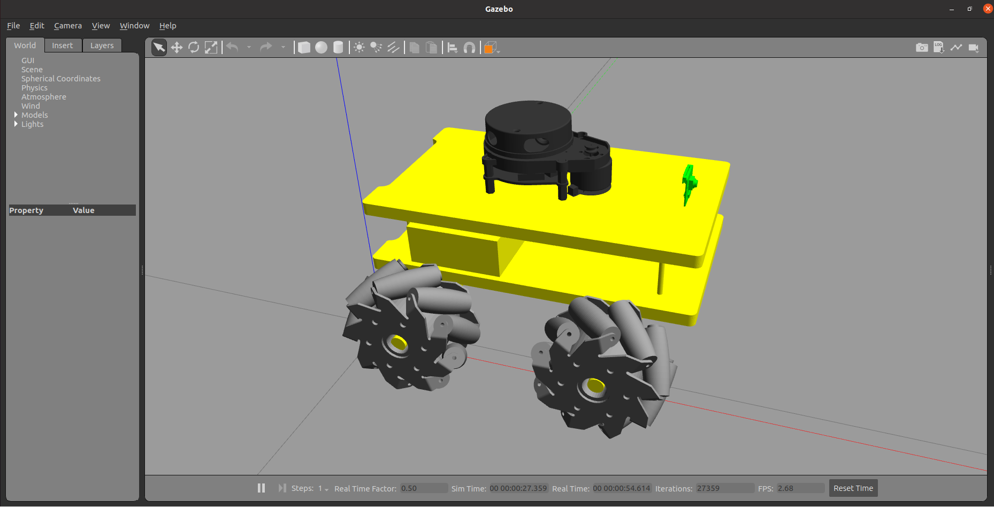
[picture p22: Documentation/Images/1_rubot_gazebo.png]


> To see the frames you have to add TF in rviz

## **2. rUBot mecanum spawn in world environment**

In robotics research, always before working with a real robot, we simulate the robot behaviour in a virtual environment close to the real one. The dynamic simulation of a robot, is a better approach to examining the actual behavior of the robot rather than just using software. Rigid body mechanics, including mass and inertia, friction, damping, motor controllers, sensor detection properties, noise signals, and every aspect of the robot and the environment that can be retained in a model with reasonable accuracy is much less expensive when replicated in a simulator than if you tried to do this with physical hardware.

Gazebo is an open source 3D robotics simulator and includes an ODE physics engine and OpenGL rendering, and supports code integration for closed-loop control in robot drives. This is sensor simulation and actuator control.

We will create a new gazebo.launch file to spawn the robot in an empty world:
```shell
roslaunch rubot_mecanum_description gazebo.launch
roslaunch rubot_mecanum_description display.launch
```

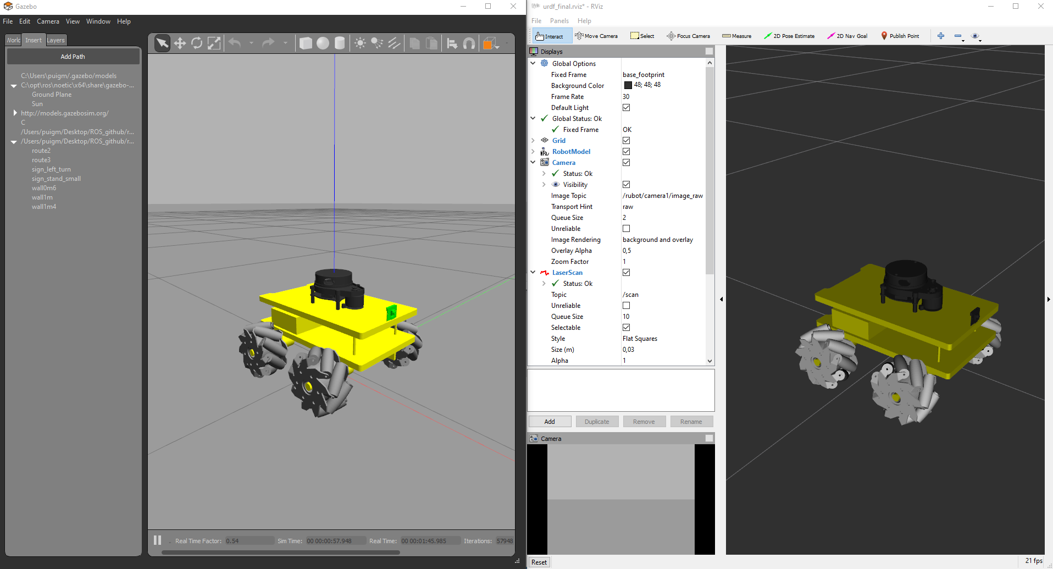
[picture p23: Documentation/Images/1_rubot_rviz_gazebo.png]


> Gazebo colors:
> - are defined at the end of URDF file
>- have a specific "Gazebo/Color" names
>- You can find the list of available Gazebo colors in: http://wiki.ros.org/simulator_gazebo/Tutorials/ListOfMaterials
```xml
  <gazebo reference="base_link">
    <material>Gazebo/Yellow</material>
  </gazebo>
  ```
> Dynamic friction coefficients:
>
> They have to be specified at the end of urdf file (zero values by default):
```xml
  <gazebo reference="upper_left_wheel">
    <material>Gazebo/Grey</material>
    <mu1>0.0</mu1>
    <mu2>0.0</mu2>
  </gazebo>
```
>Carefull-1:
- If there is an error "libcurl: (51) SSL: no alternative certificate subject name matches target host name ‘api.ignitionfuel.org’" then follow instructions:
    - Open "~/.ignition/fuel/config.yaml" (to see the hidden files type ctrl+h)
    - replace: "api.ignitionfuel.org" with "fuel.ignitionrobotics.org"
    
- information in: https://varhowto.com/how-to-fix-libcurl-51-ssl-no-alternative-certificate-subject-name-matches-target-host-name-api-ignitionfuel-org-gazebo-ubuntu-ros-melodic/

>Carefull-2: 
- In order to kill the previous Gazebo process, type:

    killall gzserver && killall gzclient

    or type ctrl+r and kill

>Carefull-3:
- Perhaps is needed to setup your Keys again:
  ```shell
  curl -s https://raw.githubusercontent.com/ros/rosdistro/master/ros.asc | sudo apt-key add -
  sudo apt get update
  sudo apt get upgrade
  ```

### **2.1. Design the Project world**

Here we have first to design the project world, for exemple a maze from where our rUBot mecanum has to navigate autonomously.

There is a very useful and simple tool to design a proper world: "Building editor" in gazebo.

Open gazebo as superuser:
```shell
sudo gazebo
```
In ROS windows:
```shell
roslaunch gazebo_ros empty_world.launch
```
You can build your world using "Building Editor" in Edit menu
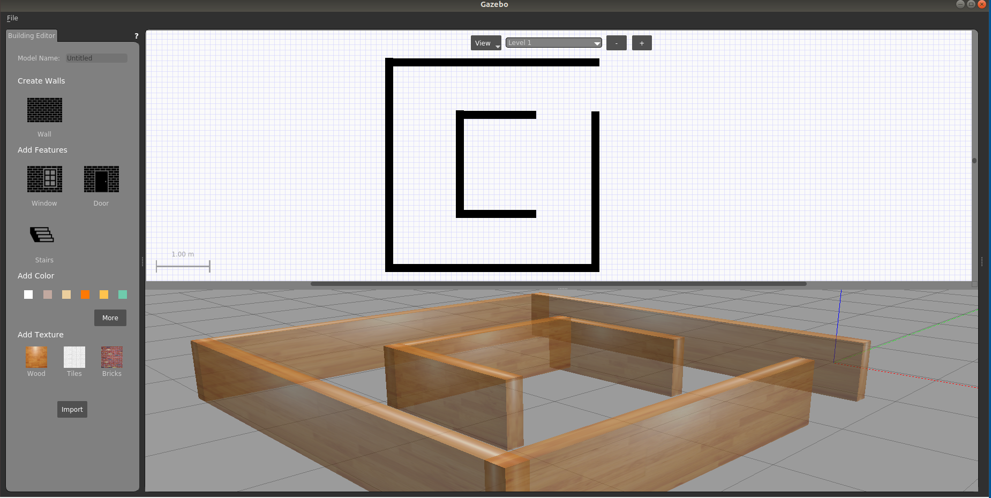
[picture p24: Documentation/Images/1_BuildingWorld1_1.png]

You can save:
- the generated model in a model folder (without extension)

Close the Builder Editor, modify the model position and add other elements if needed. Save:
- the generated world (with extension .world) in the world folder.

Once you finish is better to close the terminal you have work as superuser

#### ***Modify a created world***
- Open a terminal where you have the world you want to modify
- type: sudo gazebo ./maze1.world
- make modifications
- save your world in a Desktop directory
- close gazebo and the terminal
#### **Create world with model parts**
You can create model parts like walls of 90cm or 60cm with a geometry and color, using building editor. These parts can be saved:
- in ~/.gazebo/models/
- in speciffic folder in your package (i.e. rubot_mecanum_ws/src/rubot_projects/models), if you add this line in .bashrc file:
  ```xml
  export GAZEBO_MODEL_PATH=/media/sf_github_manelpuig/rubot_mecanum_ws/src/rubot_projects/models:$GAZEBO_MODEL_PATH
  ```
- in ROS windows terminal
  ```xml
  set GAZEBO_MODEL_PATH=/media/sf_github_manelpuig/rubot_mecanum_ws/src/rubot_projects/models
  ```
- When a model is created with "Building Editor", this path is saved in gazebo environment and you can use it in the future.

You will have acces in gazebo insert section. Then you can construct your world adding parts.

This is an exemple:


### **Exercise:**
Generate a proper world corresponding to the real world we want to spawn our rUBot mecanum robot in. For exemple a maze.

Save this world as maze.world

### **2.2. Spawn the rUBot robot in project world**

Now, spawn the rUBot mecanum robot in our generated world. You have to create a "nexus_world.launch" file:
``` shell
roslaunch rubot_mecanum_description rubot_world.launch
```


## **3. rUBot mecanum navigation control in the new world environment**

Once the world has been generated we will create a ROS Package "rubot_control" to perform the autonomous navigation
```shell
cd ~/rubot_mecanum_ws/src
catkin_create_pkg rubot_control rospy std_msgs sensor_msgs geometry_msgs nav_msgs
cd ..
catkin_make
```
### **3.1 Kinematics model of mecanum robot**
The first concept we are going to go through is kinematic models. So, we know what kinematics are, but, what is a kinematic model?

Wheeled mobile robots may be classified in two major categories, holonomic (omnidirectional) and nonholonomic. 
- Nonholonomic mobile robots, such as conventional cars, employ conventional wheels, which prevents cars from moving directly sideways.
- Holonomic mobile robots, such as mecanum cars, employ omni or mecanum wheels, which allow lateral and diagonal movements

We will define the Kinematic model for Holonomic Mecanum wheeled robot:

Omnidirectional wheeled mobile robots typically employ either omniwheels or mecanum wheels, which are typical wheels augmented with rollers on their outer circumference. These rollers spin freely and they allow sideways sliding while the wheel drives forward or backward without slip in that direction.

The different movements our car can perform are:


The forces involved define the robot linear and angular movement:


The forward Kinematic's equations are defined below:


where

- Vi: Linear speed of the wheels.
- ωdi: Angular speed of the wheels.
- Vir: Tangential speed of the rollers.
- ul: Linear velocity of the system on the X axis.
- uf: Linear velocity of the system on the Y axis.
- ω: Speed of rotation of the system on the Z axis.
- a: Distance from the center of the robot to the axis of rotation of the wheel.
- b: Distance from the center of the robot to the center of the width of the wheel.

>(see [Lynch & Park, 2017] for a complete derivation of this model).

In our case we want to apply a robot movement defined by:
- a linear and angular velocity using a Twist message type published in a /cmd_vel topic. 
- we need to calculate the 4 wheel speeds needed to obtain this robot velocity

This corresponds to an Inverse Kinematics defined by the following expressions:

With the information of (uf,ul,w) Gazebo plugin calculates to obtain the Odometry.
The analytical expressions are explained graphically in the picture:


In the case of real mecanum robot this is calculated by the robot driver as an arduino program in arduino-mega platform.

### **3.2. Mecanum control in a world environment**
We can control the movement of our robot using:
- the keyboard or a joypad
- pragramatically in python creating a "/rubot_nav" node

In any case the first step is to "bringup" our robot in the desired virtual environment. We will create a rubot_bringup.launch file to:
- Open gazebo with the desired virtual world
- spawn our robot model in a speciffic position

This file is:
```xml
<launch>
    <arg name="world" default="square2wall.world"/> 
    <arg name="model" default="rubot_rp.urdf" />
    <arg name="x_pos" default="0.8"/>
    <arg name="y_pos" default="0.0"/>
    <arg name="yaw" default="1.0"/>
    <!-- spawn world -->
    <include file="$(find gazebo_ros)/launch/empty_world.launch">
      <arg name="world_name" value="$(find rubot_mecanum_description)/worlds/$(arg world)"/>
    </include>
    <!-- spawn nexus -->
    <param name="robot_description" textfile="$(find rubot_mecanum_description)/urdf/$(arg model)" />
    <node pkg="gazebo_ros" type="spawn_model" name="spawn_model"
      args="-urdf -model rubot -x $(arg x_pos) -y $(arg y_pos) -Y $(arg yaw) -param robot_description" />
    <!-- send fake joint values -->
    <node name="joint_state_publisher" pkg="joint_state_publisher" type="joint_state_publisher">
      <param name="use_gui" value="False"/>
    </node>
    <!-- Combine joint values -->
    <node name="robot_state_publisher" pkg="robot_state_publisher" type="robot_state_publisher"/>
    <!-- Show in Rviz   -->
    <node name="rviz" pkg="rviz" type="rviz"  args="-d $(find rubot_control)/rviz/rubot_nav.rviz"/>
  </launch>
  ```
  type:
  ```shell
roslaunch rubot_control rubot_bringup.launch
  ```
  
  > In bringup file we open rviz to see the sensor messages.
  >
  > The fixed frame is now odom, then the world will not move with robot movements. We find odom frame in rviz because joint_state_publisher and robot_state_publisher are launched!

We are now ready to launch control actions

#### **3.2.1. Keyboard control**
You can control the rUBot with the keyboard installing the following packages:
```shell
sudo apt-get install ros-noetic-teleop-tools
sudo apt-get install ros-noetic-teleop-twist-keyboard
```
In ROS for windows, you need to make a source installation of this 2 packages. Follow the instructions in Documentation/Files folder to install source packages.

Then you will be able to control the robot with the Keyboard typing:
```shell
rosrun key_teleop key_teleop.py /key_vel:=/cmd_vel
or
rosrun teleop_twist_keyboard teleop_twist_keyboard.py
```
Getting Started
#### **3.2.2. Python programming control**
Diferent navigation programs are created:

- Navigation control: to define a desired robot velocity
- Lidar test: to verify the LIDAR readings and angles
- Autonomous navigation: to perform a simple algorithm for navigation with obstacle avoidance using the LIDAR
- Wall follower: at a fixed distance to perform a good map
- go to POSE: attend a specific position and orientation

The nodes and topics structure corresponds to the following picture:
Getting Started

#### **a) Navigation Control**

We will create now a first navigation python files in "src" folder:
- rubot_nav.py: to define a rubot movement with linear and angular speed during a time td

Specific launch file have been created to launch the node and python file created above:
```shell
roslaunch rubot_control rubot_nav.launch
```

#### **b) LIDAR test**

In order to navigate autonomously and avoid obstacles, we will use a specific rpLIDAR sensor.
To verify the LIDAR readings and angles we have generated the "rubot_lidar_test.py" python file:
```python
#! /usr/bin/env python3
import rospy
from sensor_msgs.msg import LaserScan
def callback(msg):
    print ("Number of scan points: "+ str(len(msg.ranges)))
    # values at 0 degrees
    print ("Distance at 0deg: " + str(msg.ranges[0]))
    # values at 90 degrees
    print ("Distance at 90deg: " + str(msg.ranges[180]))
    # values at 180 degrees
    print ("Distance at 180deg: " + str(msg.ranges[360]))
    # values at 270 degrees
    print ("Distance at 270deg: " + str(msg.ranges[540]))
    # values at 360 degrees
    print ("Distance at 360deg: " + str(msg.ranges[719]))
rospy.init_node('scan_values')
sub = rospy.Subscriber('/scan', LaserScan, callback)
rospy.spin()
```
To test the LIDAR we have generated a launch file
```shell
roslaunch rubot_control rubot_lidar_test.launch
rosrun teleop_twist_keyboard teleop_twist_keyboard.py
```

> We can see that the zero angle corresponds to the back side of the robot!

#### **c) Autonomous navigation with obstacle avoidance**
We will use now the created world to test the autonomous navigation with obstacle avoidance performance. 

We have to launch the "rubot_self_nav.launch" file in the "rubot_control" package.
```shell
roslaunch rubot_control rubot_self_nav.launch
```
>Careful:
- we have included in launch file: gazebo spawn, rviz visualization and rubot_nav node execution 
- Verify in rviz you have to change the fixed frame to "odom" frame



The algorithm description functionality is:
- "rubot_self_nav.py": The Python script makes the robot go forward. 
    - LIDAR is allways searching the closest distance and the angle
    - when this distance is lower than a threshold, the robot goes backward with angular speed in the oposite direction of the minimum distance angle.

> Note the 180 degrees turn due to the rpLIDAR orientation in rUBot:
```python
    def callbackLaser(self, scan):

        closestDistance, elementIndex = min(
            (val, idx) for (idx, val) in enumerate(scan.ranges) if scan.range_min < val < scan.range_max
        )
        angleClosestDistance = self.__wrapAngle((elementIndex / 2)-180) # RPLidar zero angle in backside

        rospy.loginfo("Closest distance of %5.2f m at %5.1f degrees.",
                      closestDistance, angleClosestDistance)
```

#### **d) Wall Follower**
Follow the wall accuratelly is an interesting challenge to make a map with precision to apply SLAM techniques for navigation purposes.

There are 2 main tasks:
- Create a python file "rubot_wall_follower.py" to perform the wall follower in the maze of our gopigo3 robot
- Create a launch file to initialyse all the needed nodes in our system for this control task

We have developed 2 different methods for wall follower:
- Geometrical method
- Lidar ranges method

#### **Geometrical method**

Follow the instructions to perform the rubot_wall_follower_gm.py python program are in the notebook: 
https://github.com/Albert-Alvarez/ros-gopigo3/blob/lab-sessions/develop/ROS%20con%20GoPiGo3%20-%20S4.md

The algorithm is based on:



A rubot_wall_follower_gm.launch is generated to test the node within a specified world
```shell
roslaunch rubot_control rubot_wall_follower_gm.launch
```

You can see a video for the Maze wall follower process in: 
IMAGE_ALT (https://youtu.be/z5sAyiFs-RU)


#### **Lidar ranges method**

We have created another rubot_wall_follower_rg.py file based on the reading distances from LIDAR in the ranges: front, front-right, front-left, right, left, back-right and back-left, and perform a specific actuation in function of the minimum distance readings.

Follow the instructions to create the rubot_wall_follower_rg.py python file: https://www.theconstructsim.com/wall-follower-algorithm/



The algorith is based on laser ranges test and depends on the LIDAR type:


```shell
roslaunch rubot_control rubot_wall_follower_rg.launch
```


#### **Go to POSE**
Define a specific Position and Orientation as a target point to go:

- x target point
- y target point
- f yaw orientation angle in deg

Modify the python script developed in turlesim control package according to the odom message type

For validation type:
```shell
roslaunch rubot_control rubot_go2pose.launch
```


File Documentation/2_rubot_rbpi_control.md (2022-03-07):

# **rUBot mecanum in Raspberrypi4 Setup&Control**

The main objectives are:
- Assemble a real robot (rUBot mecanum)
- Setup the HW drivers in raspberrypi4
- Control the rUBot movement

Let's see how to fulfill these objectives

References:
- https://github.com/ros-mobile-robots/diffbot
- https://johanschwind.medium.com/mobile-robot-teleoperation-with-the-jetson-nano-and-ros-d72b4b57e9be

## **1. rUBot assembling**

This tobot prototype is based on:
- Mecanum wheel chasis:
  - https://es.aliexpress.com/item/4001121790912.html?gatewayAdapt=glo2esp&spm=a2g0o.9042311.0.0.3c7963c0XKupJW
- Battery 12V&5V (3Ah):
  - https://www.amazon.es/gp/product/B072HR211P/ref=ppx_yo_dt_b_asin_title_o05_s00?ie=UTF8&psc=1
- Battery 12V (6,7 and 20Ah): 
  - https://www.amazon.es/gp/product/B07YSCXGNF/ref=ppx_yo_dt_b_asin_title_o07_s00?ie=UTF8&psc=1
  - https://www.amazon.es/THENAGD-Recargable-Interruptor-Encendido-DC-122000/dp/B091F465RP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
- Battery 5V (20 and 26Ah):
  - https://www.amazon.es/dp/B09MYQFXP5?psc=1&smid=AKVUAZL0K2E1J&ref_=chk_typ_imgToDp
  - https://www.amazon.es/SWEYE-Capacidad%EF%BC%BDCargador-M%C3%BAltiples-Protecciones-Smartphones/dp/B0814JMRLR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
- On-board Raspberrypi4
  - https://es.rs-online.com/web/p/raspberry-pi/2012367
  - https://es.rs-online.com/web/p/placas-hat-y-complementos-para-raspberry-pi/2208633
- Arduino mega: for HW driver control
  - https://es.rs-online.com/web/p/arduino/7154084
- Arduino motor driver shield TB6612FNG:
  - https://es.aliexpress.com/item/4001086592215.html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
  - https://github.com/Seeed-Studio/Grove_Motor_Driver_TB6612FNG
- RaspiCAM RGB camera:
  - https://es.rs-online.com/web/p/camaras-para-raspberry-pi/9132664
  - https://es.rs-online.com/web/p/cajas-para-raspberry-pi/8679049
- rpLidar:
  - https://www.robotshop.com/es/es/rplidar-a1m8-kit-desarrollo-escaner-laser-360-grados.html
- USB cables:
  - USB-A to USB-B: https://www.amazon.es/gp/product/B073XQ33L2/ref=ppx_yo_dt_b_asin_title_o01_s00?ie=UTF8&th=1
  - USB-C to USB-B: https://www.amazon.es/gp/product/B08RXQJJ9Z/ref=ppx_yo_dt_b_asin_title_o02_s00?ie=UTF8&th=1
  - microUSB to USB-B: https://www.amazon.es/gp/product/B00WMAQKS2/ref=ppx_yo_dt_b_asin_title_o04_s00?ie=UTF8&th=1

Getting Started

Other platforms:
- https://www.superdroidrobots.com/robotic-kits-platforms/mecanum-robots
- https://www.robotshop.com/es/es/kit-robot-arduino-con-rueda-mecanum-4wd-60-mm.html
- https://www.robotshop.com/es/es/4wd-robot-basico-mecanum-compatible-con-arduino.html

## **2. Setup the HW drivers in raspberrypi4**
The raspberrypi4 onboard is preinstalled with:
- Ubuntu 20 server 32bits
  - NoMachine remote desktop
- ROS Noetic
- rubot_rbpi4_ws repository is located in /home/pi/Desktop folder 

### **2.1. Install Ubuntu 20 server 32bits**

Follow the steps in order to properly install the Raspberrypi:

- Install Raspberry Pi OS using Raspberry Pi Imager (download for windows): https://www.raspberrypi.org/software/
- Run the application and save the image:
  - Ubuntu --> Ubuntu 20 server 64bits to the SD card


- Insert the SD in a RBPi board and connect it to screen and ethernet cable to the router
- power the raspberrypi4 and login:
  - login: ubuntu
  - password: ubuntu
- You will have to change the password (we use ubuntu1234)
> Note: 
> - Connect HDMI just after power rbpi4
> - Keyboard is not ESP and "-" is on "'" key

**Install Ubuntu Desktop**

In the terminal, type:
```shell
sudo apt-get install ubuntu-desktop
```
> Follow instructions:
>- Perhaps you may type "sudo dpkg --configure -a"

After some minutes, the desktop is installed. 
> You have to update and upgrade the ubuntu now (type it several times untill all packages will be updated)

Type:
```shell
reboot
```
You will get the ubuntu 20 desktop

- choose a wifi network and change the timezone, language and password

**Install nomachine remote desktop**

Download nomachine in RaspberryPi and PC:
- In raspberryPi:
  - Download the Raspberrypy4 version ARMv8 DEB in: https://www.nomachine.com/download/linux&id=29&s=Raspberry
  - open a terminal in download folder and install following the instructions
- In PC: https://www.nomachine.com/

**Notebook visualization in raspberrypi**

Use the NBviewer program from Jupyter:

https://nbviewer.ipython.org/

### **2.2. ROS Noetic Desktop installation**

Follow the instructions on: http://wiki.ros.org/noetic/Installation/Ubuntu
> Is recommended to update and upgrade first:
```shell
sudo apt update
sudo apt upgrade
sudo apt update
```
### **2.3. Create WiFi Hotspot and setup**

Follow instructions in: https://www.debugpoint.com/2020/04/how-to-create-wifi-hotspot-in-ubuntu-20-04-lts/


>Carefull!:
>- If "Turn On Wi-Fi Hotspot is disabled select another setting (i.e. Bluetooth) and come back to Wi-Fi setting
>- Choose a SSID corresponding to your robot name

To select this Hotspot automatically on restart:
- open a terminal and see all the connection names:
```shell
nmcli con show
```
- Make the connection "Hotspot" start automatically:
```shell
nmcli con mod Hotspot connection.autoconnect yes
``` 
- Verify listing all the Hotspot parameters including "autoconnect"
```shell
nmcli con show Hotspot
```
- Identify the IP of the rbpi4 Hotspot:
  - type ifconfig
  - in wlan0 you identify the inet address: 10.42.0.1

**Setup**

The raspberrypi4 is configured:
- to generate a hotspot "rUBot_xx"
- NoMachine activated 
- raspicam activated 

When powering the raspberrypi3, generates a hotspot you have to connect to:
- SSID name: rUBot_01 
- password "rUBot_Mec"

Once you are connected to this network you will be able to connect your computer to the raspberrypi4 using NoMachine viewer:
- In PC open NoMachine viewer
- Select the raspberrypi IP address: 10.42.0.1
- you have to specify:
    - user: ubuntu
    - password: ubuntu1234
- You will have the raspberrypi4 desktop on your windows NoMachine screen



If you want to change the Hotspot name (one for each robot):
- Change the Hotspot settings (name or password):
```shell
sudo nm-connection-editor
```

### **2.4. Create your workspace**

We will create the workspace where we will install all needed packages for our Hardware project
```shell
mkdir -p ~/Desktop/rubot_rbpi4_ws/src
cd ~/Desktop/rubot_rbpi4_ws/
catkin_make
echo "source ~/Desktop/rubot_rbpi4_ws/devel/setup.bash" >> ~/.bashrc
```
We will install:
- Raspberrypi camera
- rpLIDAR
- Arduino board with rosserial
### **Install raspberrypi camera**
Information is located on: https://picamera.readthedocs.io/en/release-1.11/install.html

You need to activate the raspicam in Ubuntu:
- open the file config.txt
```shell
sudo nano /boot/firmware/config.txt
```
- add the magic line start_x=1 at the end


- reboot
- update your system to install the necessary drivers:
```shell
sudo apt update
sudo apt upgrade
```
Now we will install the python module for picamera:
```shell
sudo apt install python3-pip
pip install picamera
```
And the needed libraries for raspicam package:
```shell
sudo apt-get install -y libyaml-cpp-dev
sudo apt-get install -y libogg-dev libvorbis-dev libtheora-dev
```
Finally to work with raspicam in ROS, you need to install the packages:
```shell
git clone https://github.com/UbiquityRobotics/raspicam_node.git
git clone --single-branch --branch=noetic-devel https://github.com/ros-perception/image_transport_plugins.git
git clone --single-branch --branch=noetic https://github.com/ros-perception/vision_opencv.git
git clone --single-branch --branch=noetic-devel https://github.com/ros-perception/image_common.git
```
Some dependencies have to be added.

**Instruccions Sergio!**

Follow raspicam_node --> Build Instructions in: https://github.com/UbiquityRobotics/raspicam_node

Then you are able to compile the workspace:
```shell
cd ~/Desktop/rubot_rbpi4_ws/
catkin_make
```

### **Install rpLIDAR**

Open a terminal in src folder and type:
```shell
cd ~/Desktop/rubot_rbpi4_ws/src
git clone https://github.com/Slamtec/rplidar_ros
cd ..
catkin_make
```
To test the sensor, connect the LIDAR sensor to RB Pi and execute:
```shell
roslaunch rplidar_ros view_rplidar.launch
```
### **Install ARDUINO**

This robot will be controlled by an Arduino Mega board.

The arduino program will start a serial_node with all the topics

The Arduino programm is located in "files/Arduino_node" folder.

Considering your Raspberry computer uses Ubuntu 20, as explained in previous sections, you need to download Arduino IDE version for Linux ARM 64 bits from the following link: https://www.arduino.cc/en/software.

After dowloading the zip file, reclocate it and unzip it in the Tools folder: ~/Tools/Arduino-1.8.18. From this directory, open a terminal and execute the following commands:

```shell
sudo ./install.sh
cd ~
gedit .bashrc
export PATH=$PATH:$HOME/Desktop/Arduino-1.8.18
```
Save and close the file and install rosserial for ROS Noetic using:
```shell
sudo apt-get install ros-noetic-rosserial-arduino
sudo apt-get install ros-noetic-rosserial
```
Go to ~/Desktop/Arduino-1.8.18/libraries directory and remove ros_lib folder. From this directory execute:
```shell
rosrun rosserial_arduino make_libraries.py .
```

Test Arduino ROS library with "Hello World" exemple: http://wiki.ros.org/rosserial_arduino/Tutorials/Hello%20World

### **Manage USB ports**

The rbpi4 manage arduino board and rpLIDAR with 2 USB ports. 

We have to force the same USB port to the same device:
- "arduino" port to arduino mega board
- "rplidar" port to rpLIDAR

This can be done creating UDEV rules for each devide:

**a) Arduino udev rules**

Follow instructions: 
- https://steve.fi/hardware/arduino-basics/
- https://medium.com/@darshankt/setting-up-the-udev-rules-for-connecting-multiple-external-devices-through-usb-in-linux-28c110cf9251

  Connect the Arduino Mega in USB port. To see the port name type:
  ```shell
  ls -l /dev/ttyAMC*
  ```
  Give permissions rwx to this port ttyACM*
  ```shell
  sudo chmod 777 /dev/ttyACM*
  ```
  To see the needed properties to create udev rules, type:
  ```shell
  lusb
  ```
  You will see:
  ```shell
  ubuntu@ubuntu:/usr/lib/udev/rules.d$ lsusb
  Bus 002 Device 001: ID 1d6b:0003 Linux Foundation 3.0 root hub
  Bus 001 Device 007: ID 2341:0042 Arduino SA Mega 2560 R3 (CDC ACM)
  Bus 001 Device 004: ID 0e8f:00fb GreenAsia Inc. 
  Bus 001 Device 003: ID 04d9:a01c Holtek Semiconductor, Inc. wireless multimedia keyboard with trackball [Trust ADURA 17911]
  Bus 001 Device 002: ID 2109:3431 VIA Labs, Inc. Hub
  Bus 001 Device 001: ID 1d6b:0002 Linux Foundation 2.0 root hub
  ```
  The create a file /etc/udev/rules.d/99-arduino.rules and give it the following contents:
  ```xml
  # Arduino port definition
  SUBSYSTEM=="tty", GROUP="plugdev", MODE="0660"

  ACTION=="add", SUBSYSTEMS=="usb", ATTRS{idVendor}=="2341", ATTRS{idProduct}=="0042", SYMLINK+="arduino"
  ```
  >The idProduct and idVendor corresponds to the numbers in the Arduino line.

  Now restart the service:
  ```shell
  sudo /etc/init.d/udev restart 
  ```
  Unplug and plug again the Arduino Board and verify if the symlink is created:
  ```shell
  ls -l /dev/arduino /dev/ttyACM0
  ```
  If all is OK, you will see:
  ```shell
  lrwxrwxrwx 1 root root         7 dic 23 08:58 /dev/arduino -> ttyACM0
  crw-rw---- 1 root plugdev 166, 0 dic 23 08:58 /dev/ttyACM0
  ```

**b) rpLIDAR udev rules**

Follow instructions:  
- https://github.com/Slamtec/rplidar_ros/tree/master/scripts

  Connect the rpLIDAR in USB port. To see the port name type:
  ```shell
  ls -l /dev/ttyUSB*
  ```
  Give permissions rwx to this port ttyUSB*
  ```shell
  sudo chmod 777 /dev/ttyACM*
  ```
  To see the needed properties to create udev rules, type:
  ```shell
  lusb
  ```
  You will see your rpLIDAR device properties:
  ```shell
  Bus 001 Device 010: ID 10c4:ea60 Silicon Labs CP210x UART Bridge
  ```
  The create a file /etc/udev/rules.d/rplidar.rules and give it the following contents:
  ```xml
  # set the udev rule , make the device_port be fixed by rplidar
  #
  KERNEL=="ttyUSB*", ATTRS{idVendor}=="10c4", ATTRS{idProduct}=="ea60", MODE:="0777", SYMLINK+="rplidar"
  ```
  Now restart the service:
  ```shell
  sudo /etc/init.d/udev restart 
  ```
  Unplug and plug again the Arduino Board and verify if the symlink is created:
  ```shell
  ls -l /dev/arduino /dev/ttyACM0 /dev/rplidar /dev/ttyUSB0
  ```
  If all is OK, you will see:
  ```shell
  lrwxrwxrwx 1 root root         7 dic 23 09:31 /dev/arduino -> ttyACM0
  lrwxrwxrwx 1 root root         7 dic 23 09:31 /dev/rplidar -> ttyUSB0
  crw-rw---- 1 root plugdev 166, 0 dic 23 09:31 /dev/ttyACM0
  crwxrwxrwx 1 root plugdev 188, 0 dic 23 09:31 /dev/ttyUSB0
  ```

You have now your rUBot_mecanum ready to work-with!!

### **Install joy control**

Almost all robots subscribe /cmd_vel topic whose message type is Twist for controlling robots.

Here we demonstrate how to publish Twist message to /cmd_vel using Dualshock 4 which is an official controller of PlayStation 4.

Install the following packages:
```shell
sudo apt-get install ros-noetic-joy
sudo apt-get install ros-noetic-joy-teleop
sudo apt-get install ros-noetic-teleop-tools
sudo apt-get install ros-noetic-teleop-twist-joy
```
Optional: 
- https://github.com/chrippa/ds4drv
- http://wiki.ros.org/ds4_driver

Follow indications in:
https://github.com/Utagoe-robotics/Wiki/wiki/melodic-ds4-joy

Test it using:
```shell
roslaunch teleop_twist_joy ps4_teleop.launch joy_dev:="/dev/input/js2"
```
Test the /joy and /cmd_vel topic's contents

### **Setup your workspace**

If you do not have the "rubot_rbpi4_ws" folder in your desktop, you can "transfer" folder from your PC (it takes 30s)

The first time you copy the folder, you need to compile the workspace:
- open a terminal in the ws
- type "catkin_make" (it takes 10min)

>Carefull!: Some actions have to be done:
>- review the ~/.bashrc: source to the ws and delete the environment variables
>- make executable the c++ and python files

## **3. rUBot_mecanum first control movements**
First, let's control the rUBot_mecanum movement to perform:
- movement control using keyboard
- movement control with specific python script
- autonomous navigation
- autonomous navigation following right or left wall
- Navigation to speciffic POSE

We will create a "rubot_control" package to perform the rUBot_mecanum control movements:
```shell
cd ~/Desktop/rubot_rbpi4_ws/src
catkin_create_pkg rubot_control rospy std_msgs sensor_msgs geometry_msgs nav_msgs
cd ..
catkin_make
```
First of all you need to bringup the rubot_mecanum robot.

### **3.1. Bringup rubot_mecanum**

The bringup consists to:
- launch the rUBot node in Arduino-Mega board
- launch the LIDAR node
- launch the raspicam node

**Launch rUBot node**

To bringup we need to run the driver designed for rubot_mecanum robot. The driver is in fact an arduino program that controls:
- The kinematics of the 4 mecanum wheels to apply the twist message in /cmd_vel topic
- The encoders to obtain the odometry
- Read the IMU orientation values
- interface with all the other sensors/actuators connected to arduino-mega board

The "rubot_mecanum.ino" arduino program is located on /Documentation/files/arduino/ folder

>Carefull!:
>
>You need to install Encoder.h lib: https://www.arduino.cc/reference/en/libraries/encoder/

To bringup your rubot_mecanum:
- open arduino IDE
- upload the rubot_mecanum.ino file
- Open 3 new terminals and type:
```shell
roscore
rosrun rosserial_python serial_node.py _port:=/dev/arduino _baud:=57600
rostopic pub /cmd_vel geometry_msgs/Twist -r 10 -- '[0.5, 0.0, 0.0]' '[0.0, 0.0, 0.0]'
```
> /dev/arduino is the port to which the Arduino is connected, change it in case yours is different

> The last command sends a Twist message to the robot. The wheels should be moving forward. You can try different movements by modifying the numbers inside the brackets: '[vx, vy, vz]' '[wx, wy, wz]', you should only change vx, vy and wz values as the others do not apply. As it is an holonomic robot, if all the values are 0.0 except for wz (angular velocity in z axis) you will obtain a movement in which the robot spins on itself.

**Launch LIDAR node**

To launch the rpLIDAR sensor, connect the LIDAR sensor to RaspberryPi and execute:
```shell
roslaunch rplidar_ros rplidar.launch
```
**Launch raspicam node**

To launch the raspicam sensor, execute:
```shell
roslaunch raspicam_node camerav2_410x308_30fps.launch enable_raw:=true camera_frame_id:="laser_frame"
```
> Change the launch file for image resolution and frame rate

**Final bringup launch file**

We will create a "rubot_bringup.launch" file to setup the rUBot_mecanum.
```xml
<launch>
 <!-- launch rUBot mecanum   -->
  <node name="serial_node" pkg="rosserial_python" type="serial_node.py">
    <param name="port" type="string" value="/dev/arduino"/>
    <param name="baud" type="int" value="57600"/>
  </node>
 <!-- launch ydlidar   -->
  <include file="$(find rplidar_ros)/launch/rplidar.launch"/>
  <!-- launch raspicam   -->
  <include file="$(find raspicam_node)/launch/camerav2_410x308_30fps.launch">
	<arg name="enable_raw" value="true"/>
	<arg name="camera_frame_id" value="base_scan"/>
  </include>
</launch>
```

### **3.2. Movement control using keyboard**

To control the gopigo robot with keyboard, we need to install "teleop_tools" package. Open a new terminal and install the packages:
```shell
sudo apt-get install ros-noetic-teleop-tools
sudo apt-get install ros-noetic-teleop-twist-keyboard
```
Proceed with:
- Bringup rUBot_mecanum
```shell
roslaunch rubot_control rubot_bringup.launch
```
- Then open a new terminal and type:
```shell
rosrun key_teleop key_teleop.py /key_vel:=/cmd_vel
or
rosrun teleop_twist_keyboard teleop_twist_keyboard.py
```

### **3.3. Movement control with python script**

From the "rubot_rbpi4_ws" workspace, the src/rubot_control folder has 2 new folders:
- scrip folder: with the python programs for specific movement control
- launch folder: with programs to launch the movement control

Diferent navigation programs are created:

- Navigation control: to define a desired robot velocity
- Lidar test: to verify the LIDAR readings and angles
- Autonomous navigation: to perform a simple algorithm for navigation with obstacle avoidance using the LIDAR
- Wall follower: at a fixed distance to perform a good map
- go to POSE: attend a specific position and orientation

The nodes and topics structure corresponds to the following picture:
Getting Started

### **a) Navigation control**

We have created a first navigation python files in "src" folder:

- rubot_nav.py: to define a rubot movement with linear and angular speed to reach a maximum x-distance
- rubot_nav1.py: to define the movement with vx, vy and w to reach a maximum distance in x or y

A "rubot_nav.launch" and "rubot_nav1.launch" files have been created to launch the node and python file created above.

To properly perform a especific movement control we have first to:
- Bringup rUBot_mecanum
```shell
roslaunch rubot_control rubot_bringup.launch
```
- Then open a new terminal to launch the rUBot_nav node to perform the specific movement control.
```shell
roslaunch rubot_control rubot_nav.launch
```

### **b) LIDAR test**

In order to navigate autonomously and avoid obstacles, we will use a specific rpLIDAR sensor. To verify the LIDAR readings and angles we have generated the "rubot_lidar_test.py" python file:

To properly perform a especific movement control we have first to:
- Bringup rUBot_mecanum
```shell
roslaunch rubot_control rubot_bringup.launch
```
- Then open a new terminal to launch the rUBot_nav node to perform the rpLIDAR test. We have created specific python file and launch file for this test control
```shell
roslaunch rubot_control rubot_lidar_test.launch
rosrun teleop_twist_keyboard teleop_twist_keyboard.py
```
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

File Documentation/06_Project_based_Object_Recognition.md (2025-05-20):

# Project based on Object recognition

We will describe the Computer Vision based method to identify the Traffic Sign

## ROS packages installation

The needed packages installation instructions:
````shell
sudo apt-get update
sudo apt-get install python3-opencv
sudo apt install python3-pip
sudo pip install numpy matplotlib
sudo pip install keras
sudo pip install tensorflow
````
We will use Keras that is a high-level API that runs on top of TensorFlow. By using both TensorFlow and Keras, you get the best of both worlds: the ease of use and simplicity of Keras, combined with the power and flexibility of TensorFlow. 

## Getting started

1. Bringup the rUBot:
   ```bash
   roslaunch rubot_mecanum_description rubot_bringup_HW_arduino.launch
   ````
   > Remember this is already done if you are using the bringup service
2. Place the rUBot in front of the Traffic Signal:
   
   You will create a set of around 100 photos for each traffic signal and you will copy the photos for each traffic signal in a local PC folder with a custom name (Stop, Turn_Right, Turn_Left, forbidden direction, give way, etc)

3. Open RVIZ to see the picture frame
    ````bash
    rviz
    ````
    > Add the topic /usb_cam/image_raw/Image to see the camera view before starting the 'take_photo' node
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

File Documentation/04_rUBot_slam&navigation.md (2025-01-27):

# **SLAM & Navigation rUBot mecanum**
Autonomous navigation refers that the robot is able to move autonomously around the environment avoiding any obstacle.

In a logistics warehouse, a delivery robot carries samples or food from one room to another. 

The main objectives are:
- use SLAM (Simultaneous Localization and Mapping) techniques to generate and store a map of the logistics warehouse flor
- use Navigation techniques to find an optimal trajectory to reach a speciffic logistics warehouse target position

SLAM is a technique used in robotics to explore and map an unknown environment while estimating the pose of the robot itself. As it moves all around, it will be acquiring structured information of the surroundings by processing the raw data coming from its sensors.

let's see how to fulfill these objectives
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

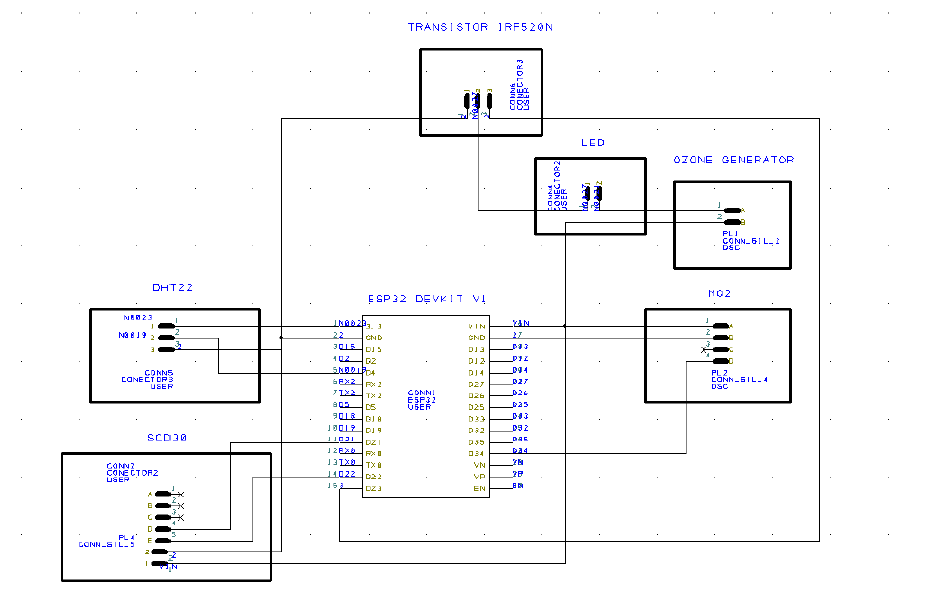
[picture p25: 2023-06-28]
Documentation/Images/10_Air_Quality/schematic.PNG

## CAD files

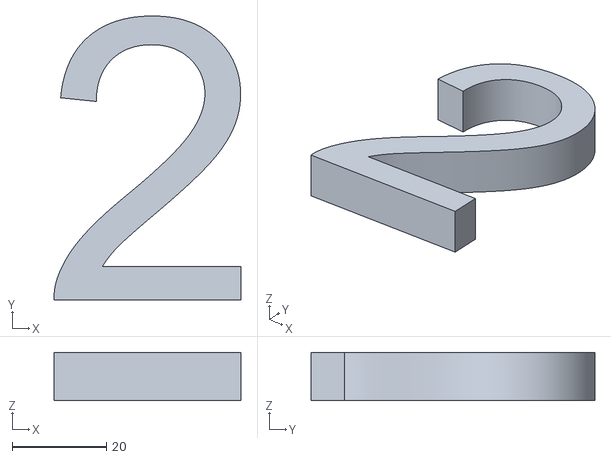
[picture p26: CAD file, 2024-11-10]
src/rubot_mecanum_description/meshes/rubot/number2.stl
39.7 x 60.2 x 10.2

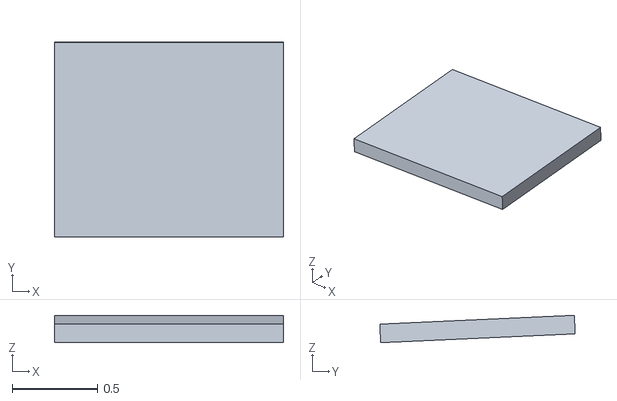
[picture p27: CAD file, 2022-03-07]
src/rubot_mecanum_description/models/sign_left/meshes/sign_board.obj
1.34 x 1.14 x 0.16

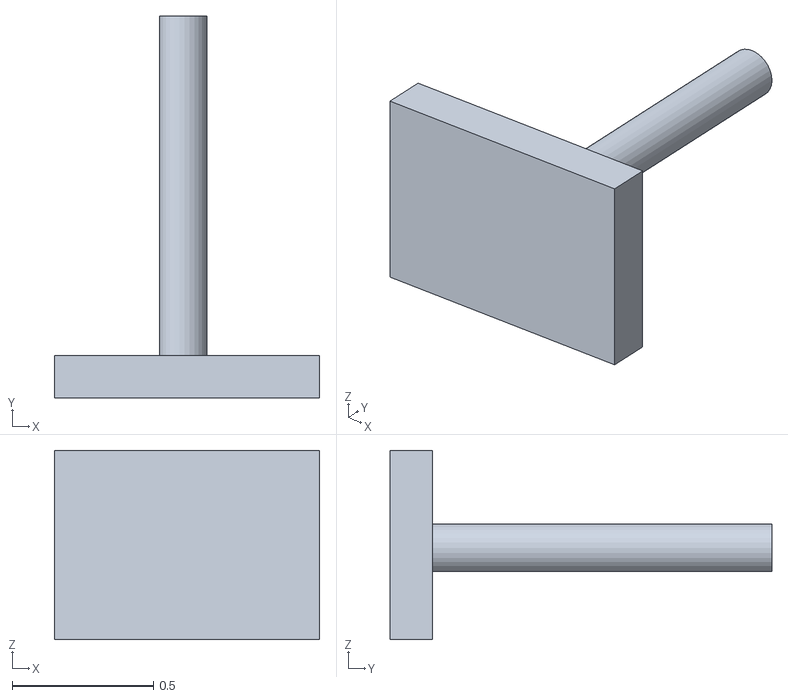
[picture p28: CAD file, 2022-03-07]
src/rubot_mecanum_description/models/sign_right/meshes/sign_stand.obj
0.937 x 1.35 x 0.668

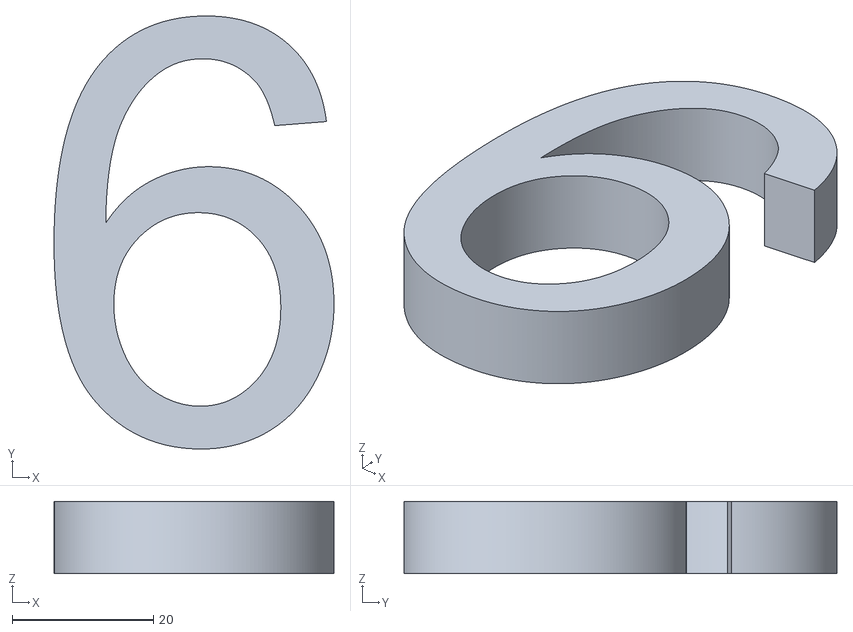
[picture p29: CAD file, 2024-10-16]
src/rubot_mecanum_description/meshes/rubot/number6.stl
39.6 x 61.3 x 10.2

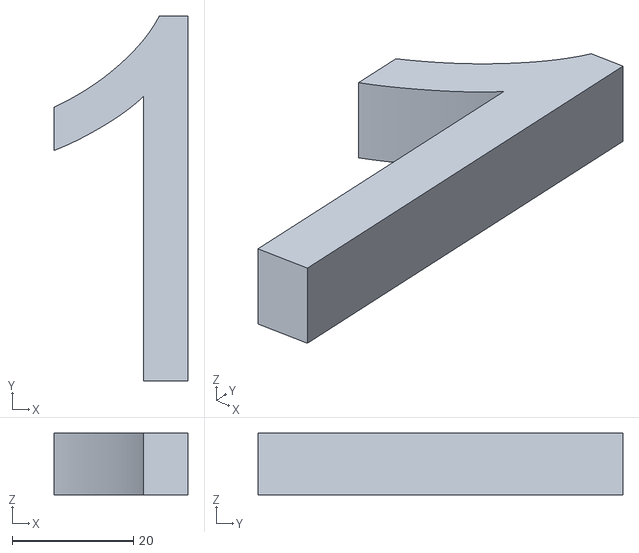
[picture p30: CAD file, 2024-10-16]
src/rubot_mecanum_description/meshes/rubot/number1.stl
22.1 x 60.2 x 10.2

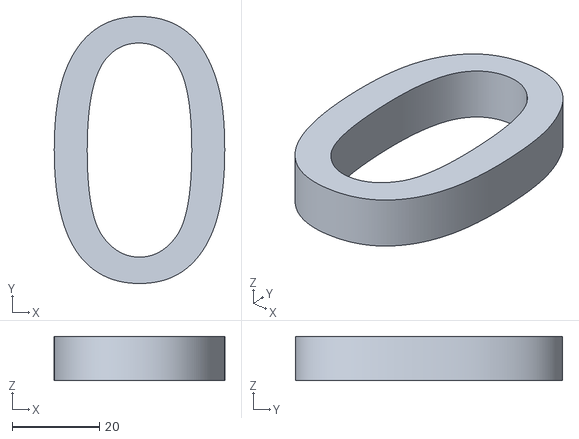
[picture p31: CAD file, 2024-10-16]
src/rubot_mecanum_description/meshes/rubot/number0.stl
39.1 x 61.3 x 10.2

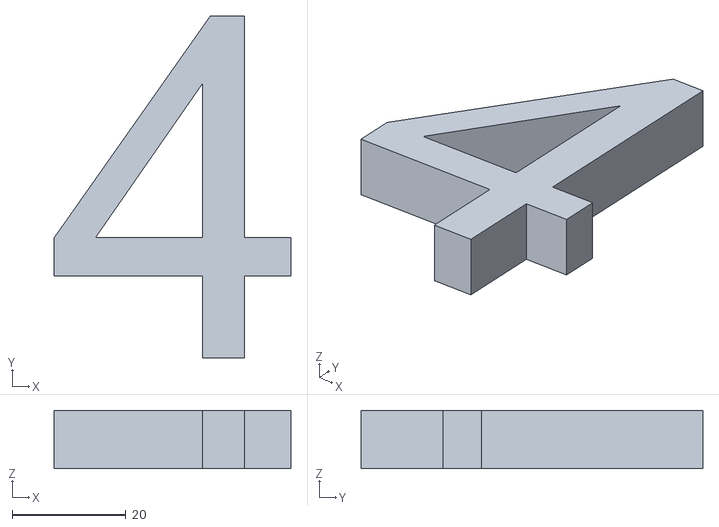
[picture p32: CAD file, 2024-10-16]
src/rubot_mecanum_description/meshes/rubot/number4.stl
41.5 x 60.0 x 10.2

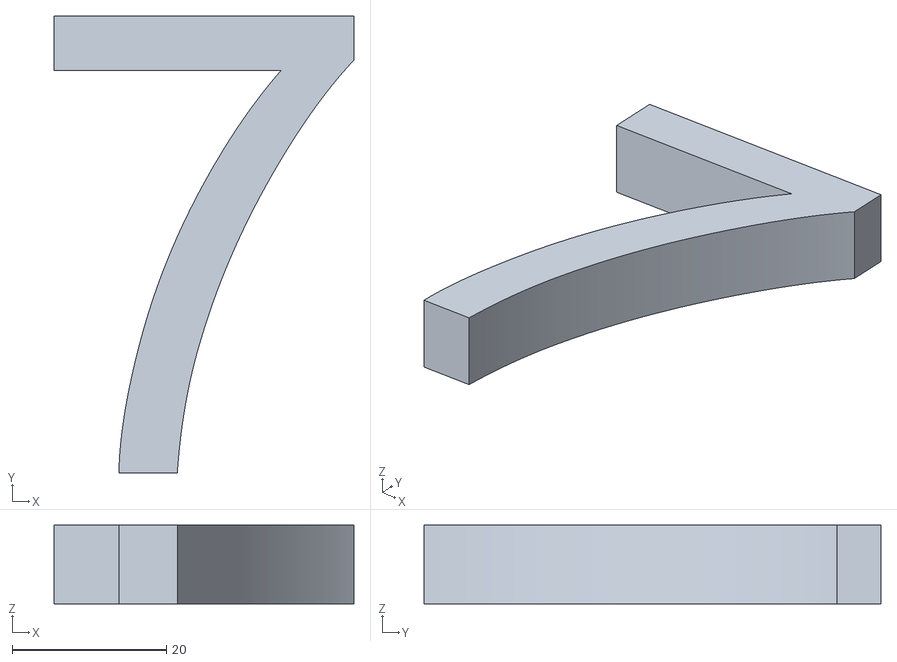
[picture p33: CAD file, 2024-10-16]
src/rubot_mecanum_description/meshes/rubot/number7.stl
38.8 x 59.2 x 10.2

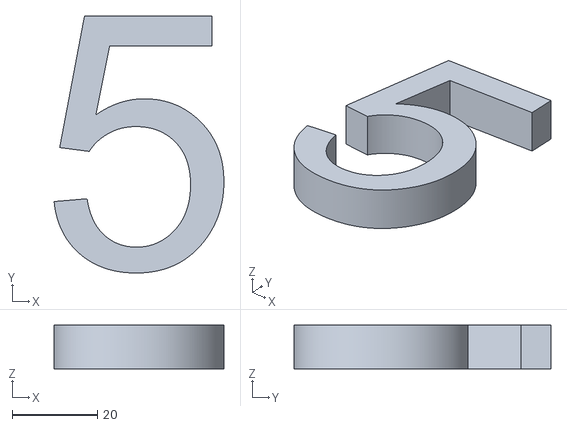
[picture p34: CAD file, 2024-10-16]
src/rubot_mecanum_description/meshes/rubot/number5.stl
39.8 x 60.2 x 10.2

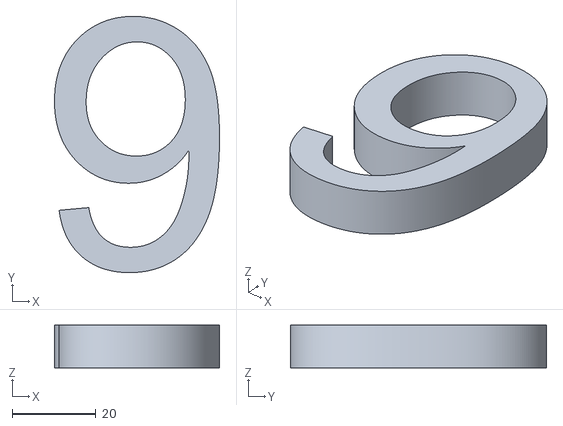
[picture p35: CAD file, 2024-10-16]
src/rubot_mecanum_description/meshes/rubot/number9.stl
39.5 x 61.3 x 10.2

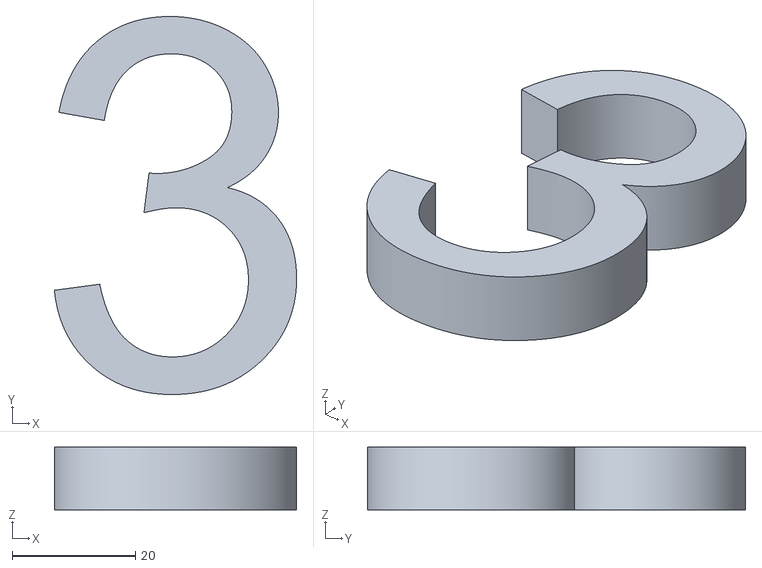
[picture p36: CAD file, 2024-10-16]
src/rubot_mecanum_description/meshes/rubot/number3.stl
39.3 x 61.3 x 10.2

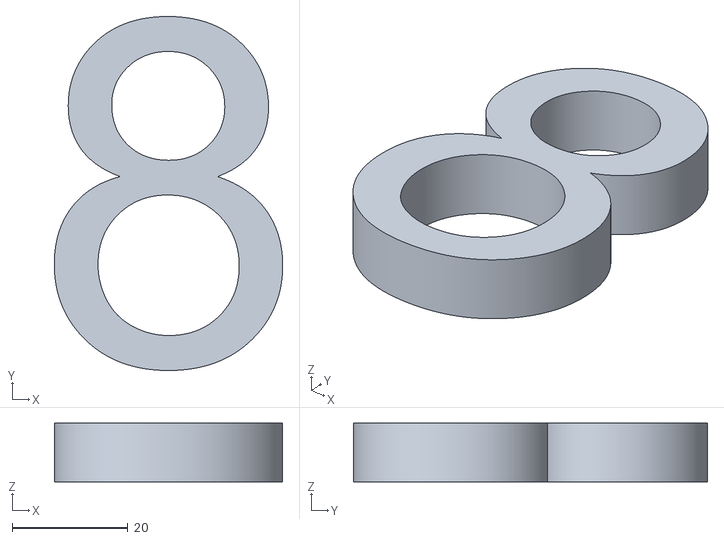
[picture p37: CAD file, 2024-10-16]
src/rubot_mecanum_description/meshes/rubot/number8.stl
39.5 x 61.3 x 10.2

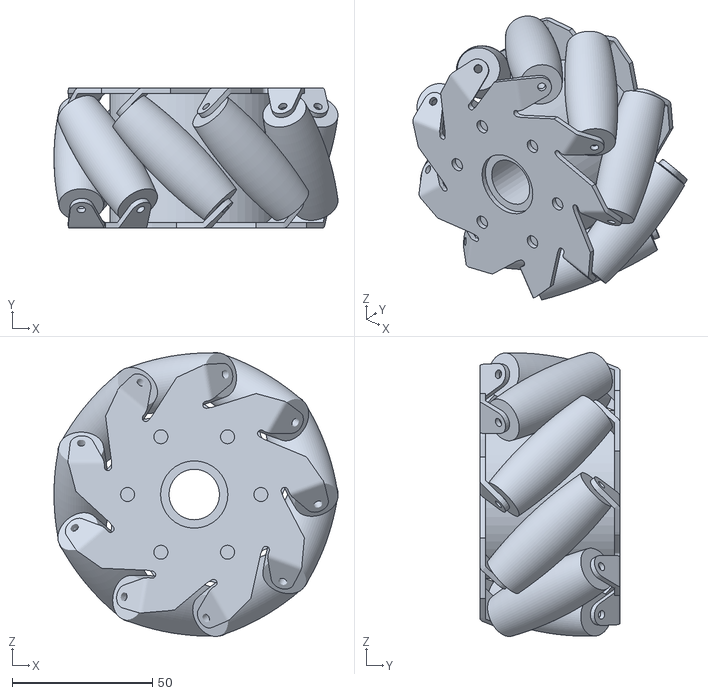
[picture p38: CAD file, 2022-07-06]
src/rubot_mecanum_description/meshes/rubot/upper_right_wheel.stl
101.2 x 50.0 x 101.3

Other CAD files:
src/rubot_mecanum_description/meshes/rubot/upper_left_wheel.stl
src/rubot_mecanum_description/meshes/rubot/lower_left_wheel.stl
src/rubot_mecanum_description/meshes/rubot/lower_right_wheel.stl

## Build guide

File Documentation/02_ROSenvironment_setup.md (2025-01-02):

# **ROS environment setup**

The rUBot mecanum robot we will work is represented in the picture:

His main characteristics are: 

- RaspberryPi4 computer onboard control with Ubuntu20 and ROS Noetic
  - RPlidar distance sensor
  - usb camera sensor
- Arduino MEGA with shield for sensors & actuators control
  - Servomotor actuators for the 4 mecanum wheels
  
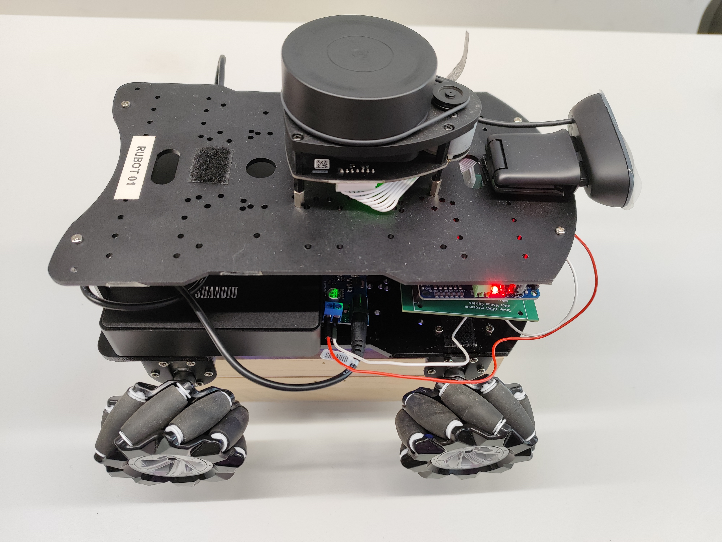
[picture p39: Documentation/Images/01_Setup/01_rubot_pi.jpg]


The main objectives of this chapter are:

- Setup the ROS environment to work with rUBot_mecanum_ws in simulation mode
- Connect the ROS environment with the real rUBot_mecanum

There are different possible solutions for the ROS environment in function of how the real robot is configured:

- If the **rUBot** is connected to a Public Network (recommended)
- If the **rUBot** starts a local hotspot

**Bibliography:**
- https://bitbucket.org/theconstructcore/workspace/projects/PS
- Arduino original program: https://blog.csdn.net/baidu_23831861/article/details/106938752

## **1. rUBot is connected to a Public Network**

When real rUBot is connected to a Public Nerwork we can connect to the real rUBot using:
  - TheConstruct ROS Environment (recommended)
  - WSL ROS environment
  - Docker ROS environment

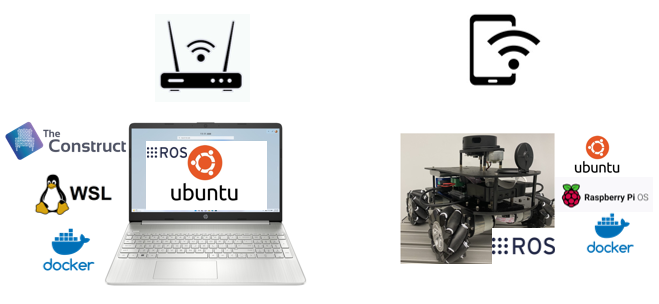
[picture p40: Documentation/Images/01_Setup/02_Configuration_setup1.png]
  

### **2.1.1. TheConstruct ROS Environment (recommended)**

To **setup the repository** in your ROS environment, you need to:
- Fork my repository in your github account
- Open your ROS Noetic environment: https://app.theconstructsim.com/
- Clone your forked directory in your home directory
  ```shell
  cd /home/user
  git clone https://github.com/yourusername/rUBot_mecanum_ws
  cd rUBot_mecanum_ws
  catkin_make
  ```
- Open .bashrc file with VS Code (open file...)
- Ensure that you have the last 2 lines (review the exact name of your repository):
  ```shell
  source /opt/ros/noetic/setup.bash
  source /home/user/rUBot_mecanum_ws/devel/setup.bash
  ```
You are ready to work with your repository!

To **sync the repository** with the one in your github account, follow the instructions:
- Access to the TheConstruct environment local repository:
  ````shell
  cd /local repository path
  ````
- Update the local repository with possible changes in github origin repository
  ````shell
  git pull
  ````
- You can work with your local repository for the speciffic project session
- Once you have finished and you want to syncronize the changes you have made and update the github origin repository, type:
  ````shell
  git add .
  git commit -m "Message"
  git push
  ````
- You will have to specify the Username and Password (Personal Access Token you have generated)

To obtain the **PAT** in github follow the instructions:

- Log in to GitHub
- Go to Developer Settings
- Select Access Personal Access Tokens: Choose Tokens (classic)
- Click Generate new token (classic) and configure it:
  - Add a note to describe the purpose of the token, e.g., "ROS repo sync."
  - Set the expiration (e.g., 30 days, 60 days, or no expiration).
  - Under Scopes, select the permissions required:
    - For repository sync, you usually need: repo (full control of private repositories)
  - Click Generate token
- Once the token is generated, copy it immediately. You won't be able to see it again after leaving the page.

Your github origin repository has been updated!

To **connect your rUBot mecanum**  to the TheConstruct environment you have to configure your robot to be used in your ROSject. 

The **Instructor** will configure the rUBot:
- In the master **TheConstruct account**, we have to first add a new robot:
  - Open the TheConstruct account and choose "Real Robots". Here you can add your robot.
  - Specify the name and the ROS version
  - Copy the "robot setup code line" used later to setup the robot to the TheConstruct environment

- In the **VScode terminal on rUBot-raspberrypi**:
  - Remember to be connected temporally to the same network as the real rUBot.
  - It is better first to update and upgrade the ubuntu20
  - Paste the "robot setup code line". After some minutes the robot will be properly installed.
  - Run 'source ~/.bashrc' to re-export ROS variables before running roscore.
  - Bringup the robot. This will be done automatically every time the robot is swhitched on.

The **students** will be able to connect to specific real robot:
- Connect to the proper account: robotics.ub1@gmail.com
- In the **TheConstruct environment ROS_Noetic_course** from "my ROSjects": 
  - Select "Real robots", select the rUBot you have configured previously and "connect"
  - You can control the robot from the same TheConstruct environment you are using for simulation

The real rUBot is usually connected to a public network with "robotics_ub" hotspot and the ROS environment is installed in a PC connected to a public network (the same "robotics_ub" or a different one).

### **2.1.2 WSL ROS environment**

Windows Subsystem for Linux is a good method to install a Linux Virtual Machine with ROS in a **windows PC**.

You will have to download and install Ubuntu from Microsoft store

You will have a **fast** and robust ROS environment in your windows PC

To properly work with WSL, use VScode with "Remote Explorer" extension installed:
- Open VS code and select "Remote Explorer"
- Select "WSL targets" and the "ubuntu20" 
- Connect to a new window
- Install ROS

To finish, in a VScode choose "Close remote connection"

You will be automatically disconnected from WSL Virtual machine.

To work with a **real rUBot**, connect your computer to the same Public Network your robot is connected to.

Using VS code with "Remote Explorer" extension installed:
- Open VS code and select "Remote Explorer"
- Select "WSL targets" and the "ubuntu20" 
- Connect to a new window

To control your real rUBot, you will have to specify that:

- The master is running in the rUBot board
- Your ROS environment is located in another PC

You will have to configure:
- The .bashrc from rUBot raspberrypi board with:
  ````shell
  export ROS_MASTER_URI=http://localhost:11311
  export ROS_IP=localhost
  ````
- The .bashrc from PC ROS environment with (obtained with a cmd):
  ````shell
  export ROS_MASTER_URI=http://<raspberry_pi_ip>:11311
  export ROS_IP=<WSL2_ip>
  ````
- Verify that the rUBot has started the Bringup
- Start XLaunch on your Windows PC for graphical interface and configure it with these settings:
    - Select "Multiple windows" or "One large window", depending on your preference.
    - Set Display number to 0 (default).
    - Enable "No Access Control" if you're having trouble connecting. This is less secure but helpful for initial setup and debugging.
    - Click Next and complete the setup.
- Verify the DISPLAY variable
Now you can control and view graphic windows with your PC under WSL ROS Virtual Machine! 

To finish, follow the steps:
- in a VScode rUBot terminal type:
  ````shell
  sudo poweroff
  ````
- in VS code choose "Close remote connection"

You will be automatically disconnected from VS code and after 1 minute, you can switch off the raspberryPi.

### **2.1.3. Using Docker ROS environment**

Docker is also a good option to install a ROS Virtual machine. This is compatible for Windows and MAC.

You will have to:
- Download and install Docker: https://docs.docker.com/desktop/setup/install/windows-install/
- All official Docker Images available are located in: [DockerHub](https://hub.docker.com/)
- Create a container with name, graphical display and Interactivelly type:
  ````shell
  docker run -it --name ros_noetic_desktop_rubot_container --env DISPLAY=host.docker.internal:0.0 --network=host --privileged ros_noetic_desktop_rubot /bin/bash
  ````
- Start XLaunch on your Windows PC for graphical interface and configure it with these settings:
    - Select "Multiple windows" or "One large window", depending on your preference.
    - Set Display number to 0 (default).
    - Enable "No Access Control" if you're having trouble connecting. This is less secure but helpful for initial setup and debugging.
    - Click Next and complete the setup.

- From VScode select Docker Extension and attach to the new running container and open folder in /root. 

You are now ready to work on your custom ROS container with graphical display!

To Exit the container:
- Close remote connection in VScode attached to Container
- In PC VScode terminal on container, type "exit"
- You can also user the Docker Extension to start and stop the container

To control the **real rUBot** you will have to connect your PC to the same Public Network your real rUBot is connected to.

You will have to specify that:

- The master is running in the rUBot board
- Your ROS environment is located in another PC

You will have to configure:
- The .bashrc from rUBot raspberrypi board with:
  ````shell
  export ROS_MASTER_URI=http://<raspberry_pi_ip>:11311
  export ROS_IP=<raspberry_pi_ip>
  ````
- The .bashrc from PC ROS environment with:
  ````shell
  export ROS_MASTER_URI=http://<raspberry_pi_ip>:11311
  export ROS_IP=<Docker_ip>
  ````
Now you can control and view graphic windows with your PC under Docker container!

## **2. rUBot starts a local hotspot**

When real rUBot starts a local hotspot, we can connect to the real rUBot using:
  - Remote Desktop
  - VScode with grahical interface

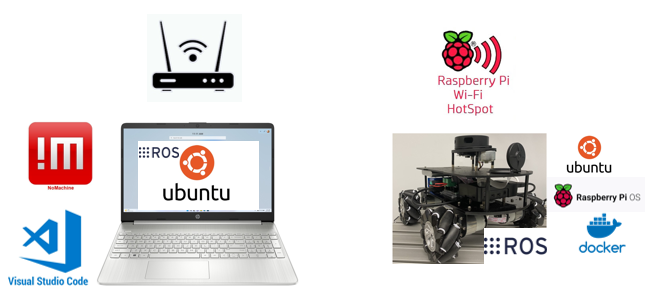
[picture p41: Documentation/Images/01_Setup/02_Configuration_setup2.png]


### **2.1 Remote Desktop**

To connect your PC to the Robot Hotspot, we have to select the rubot hotspot network:
  - SSID name: rubot_XX 
  - password "rUBot_Mec"

We will use Nomachine as a remote Desktop, select:
- IP address: 10.42.0.1
- user: ubuntu
- password: ubuntu1234

For a proper Display resolution in Nomachine, select: Display --> Change the size of remote screen

You will have the rUBot desktop on your windows nomachine screen

You are ready to work for the laboratory session!

### **2.2. VS code with graphical display**

To connect your computer to the robot using VS code with "Remote Explorer" extension installed:
- Open VS code and select "Remote Explorer"
- Add a new SSH connection as: "ssh -X ubuntu@10.42.0.1"
- Verify on ssh/settings "ForwardX11 yes" and "user ubuntu" 
- After connection specify the password as "ubuntu1234"

>Note: When you connect to your rUBot from another computer, you will have perhaps to regenerate the KEYS. In a new cmd on your PC, type the instuction and you will be able to connect with VScode:
````shell
ssh-keygen -R 10.42.0.1
````

You are now inside the rUBot_xx raspberrypi!

To finish, follow the steps:
- in a VScode rUBot terminal type:
````shell
sudo poweroff
````
- in VS code choose "Close remote connection"

You will be automatically disconnected from VS code and after 1 minute, you can switch off the raspberryPi.

**Graphical display**
To have graphical display we need:
- In your PC: Install Xlaunch
  - Download and install "Xming X Server for Windows" from: https://sourceforge.net/projects/xming/
  - Start XLaunch and in first window choose "Multiple windows" and Display "0"
  - in second window select "Start no client".
  - In the third window, ensure that "Disable access control" is selected (this allows your Raspberry Pi to connect).
  - Finish the setup and let XLaunch run in the background.
- Obtain the IP of your PC using "cmd" and type "ipconfig" (i.e. 10.42.0.78)
- In VScode raspberrypi4:
  - update and upgrade the raspberrypi ubuntu
  - Perhaps the firewall will block the connection, you have to create a new firewall rule:
    - Open the Windows Defender Firewall settings.
    - Go to Advanced Settings.
    - Create a new inbound rule:
      - Rule Type: Custom
      - Program: All programs
      - Protocol: TCP
      - Local Port: All ports
      - Remote IP Address: 10.42.0.0/24
      - Action: Allow the connection
      - Profile: Check only "Private" to allow traffic when connected to private networks.
  - reboot
  - Add to .bashrc file the lines: 
  ````shell
  export DISPLAY=10.42.0.78:0.0
  source /opt/ros/noetic/setup.bash
  source /home/ubuntu/Desktop/rUBot_mecanum_ws/devel/setup.bash
  ````

Graphical windows will be displayed in your PC Display!

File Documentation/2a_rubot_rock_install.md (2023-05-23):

# **rUBot mecanum in Rock Install**

The main objectives are:

- Setup the HW drivers in rock4 SE
- Control the rUBot movement

Let's see how to fulfill these objectives

References:

## **1. Setup the rubot in rock4**
You can connect to the rock4 onboard with:
- Nomachine remote desktop
- Visual Studio Code

### **1.1. Setup the rubot in rock4 using nomachine remote desktop**
The rock4 onboard is preinstalled with:
- Ubuntu 20 server 64bits
- NoMachine remote desktop
- ROS Noetic

> **Important!**: in order to have available all the USB connectors, commute the switch to the position closer to USB3. This control the USB mode from Device to Host.

**Remote desktop**

In order to have remote access within Nomachine you have to:

- Install the package: xserver-xorg-video-dummy
```shell
sudo apt install xserver-xorg-video-dummy
```
- Create a configuration file at "/usr/share/X11/xorg.conf.d" folder
```shell
sudo mousepad /usr/share/X11/xorg.conf.d/20-dummy.conf
```
- This file has the contents:
```python
Section "Monitor"
   Identifier "Monitor0"
   HorizSync 28.0-80.0
   VertRefresh 48.0-75.0
   Modeline "1920x1080_60.00" 172.80 1920 2040 2248 2576 1080 1081 1084 1118 -HSync +Vsync
EndSection

Section "Device"
   Identifier "Card0"
   Driver "dummy"
   VideoRam 256000
EndSection

Section "Screen"
   DefaultDepth 24
   Identifier "Screen0"
   Device "Card0"
   Monitor "Monitor0"
   SubSection "Display"
     Depth 24
     Modes "1920x1080_60.00"
   EndSubSection
EndSection
```
- reboot

- In your computer choose the rock4 hotspot:
  - SSID: rubot_00
  - Password: rockubuntu1234

- Open Nomachine and connect to rock4 with:
  - IP: 10.42.0.1
  - port: 4000
  - user: pi
  - password: rockbian

- You will need to change the Keyboard to Spanish keyboard. 
```shell
sudo setxkbmap -layout 'es,es' -model pc105
setxkbmap es sundeadkeys
```
- Change to a bash terminal:
```shell
bash
```
- Open .bashrc and add:
```shell
source /opt/ros/noetic/setup.bash
```
You will have remote connection within Nomachine with an optimized resolution!

**Wifi access**

In order to have wifi access we will use a generic wifi dongle and install a specific driver:
- https://github.com/morrownr/8821au-20210708

Follow instructions for installation within Ubuntu.

**Install VS Code**

You need to:
- download the linux .deb arm64 program version in: https://code.visualstudio.com/#alt-downloads
- Install with terminal instruction:
```shell
sudo apt install ./code_arm64.deb
```
  >Use the name of the deb file downloaded
- You will see the Code program in the Ubuntu programs available

**Sync your github repository with VS Code**

Once updated the repository in rock4 board and with ethernet connection:
- add "Git Extension Pack"
- Select "source control"
- Select the changes to sync and add commit
- Select sync and follow the instructions
  - accept communication with github
  - insert your username and password of your github account
  - accep git authorisation when prompted

You will be able to update your github repository!
### **1.2. Connection using VS Code**
You need the latest version (1.75.1).

First time you will need to connect the rock-board to internet with ethernet cable ti install some capabilities.

Install the extensions.
- Remote development
- Git Extension Pack (in your remote 10.42.0.1 board)

The first time you connect the VS Code to the Remote machine:
- You will need to sign autorization to VS code to access github (will be in left-side bar menu, accounts symbol)
- When sync the changes, you will have to type your email and user name (following the git output information)
- You can work without internet connection, but When you want to sync your repository you will need the ethernet cable connected.

Follow the instructions:
- In windows open VS Code as administrator
- Select the rUBot_XX wifi network 
- From "remote Explorer" (left-side bar menu) select "Remote" and type the IP
- Select linux system for remote connection
- type the password

You will have the VS Code attached to remote machine (rock board)

You will be able to perform all in rock4 board but you will not have screen monitor graphic service

## **2. Setup the rubot in rock5**

The rock5 image is preinstalled with:
- Ubuntu 20 server 64bits

Insert the SD card in rock5b board and power it. 

You will be asked for:
- login: rock
- password: rock

Now we have to update the public key of radxa apt. The one used before is expired. (https://github.com/radxa/apt)

You can execute the following command to get the new available.
```shell
sudo apt-get install -y wget
export DISTRO=focal-stable
wget -O - apt.radxa.com/$DISTRO/public.key | sudo apt-key add -
sudo apt update
sudo apt upgrade
```

You will need to install:
- Ubuntu-desktop
- nomachine
- Access to Remote desktop

### **2.1. Install Ubuntu-desktop**

In the terminal, type:
```shell
sudo apt update
sudo apt install ubuntu-desktop
```
Now reboot

### **2.2. Hotspot configuration**
With internet connection, install hostapd
```shell
sudo apt install hostapd
```

In Ubuntu desktop, select "Configuration settings" --> "network" and select "hotspot"

If you want to change the Hotspot name (one for each robot):

Change the Hotspot settings (name or password):
```shell
sudo nm-connection-editor
```
To select this Hotspot automatically on restart:

- open a terminal and see all the connection names:
```shell
nmcli con show
```
- Make the connection "Hotspot" start automatically:
```shell
nmcli con mod Hotspot connection.autoconnect yes
```
- Verify listing all the Hotspot parameters including "autoconnect"
```shell
nmcli con show Hotspot
```

- Identify the IP of the rbpi4 Hotspot: 
  - type ifconfig
  - in wlan0 you identify the inet address: 10.42.0.1

### **2.3. Install nomachine**
You have to install ARM version: https://downloads.nomachine.com/download/?id=114&distro=ARM

In the terminal, type:
```shell
sudo dpkg -i nomachine_8.4.2_1_arm64.deb
```
>Verify the correct syntax of nomachine version

### **2.4. Access to Remote desktop**
In order to have remote access within Nomachine you have to:

- Install the package: xserver-xorg-video-dummy
```shell
sudo apt install xserver-xorg-video-dummy
```
- Create a configuration file at "/usr/share/X11/xorg.conf.d" folder
```shell
sudo gedit /usr/share/X11/xorg.conf.d/20-dummy.conf
```
>Copy the same contents as the rock4 case

### **2.5. Install VS Code**
Open web browser and find VS Code DEB version for Ubuntu in ARM64
- Download and install:
```shell
sudo apt install ./codexxx.deb
```
- Clone the repository to work with
- Make changes and sync
- Follow instructions to insert your email and name
- when syncing you will have to insert ypur github account name and password

### **2.6. Install Arduino**
Open web browser and download the linux arm64bits version
```shell
https://www.arduino.cc/en/software
```
After downloading the zip file, realocate it and unzip it in the Tools folder: ~/Desktop/Arduino. From this directory, open a terminal and execute the following commands:

```shell
sudo ./install.sh
cd ~
gedit .bashrc
export PATH=$PATH:$HOME/Desktop/Arduino
```
Save and close the file and install rosserial for ROS Noetic using:
```shell
sudo apt-get install ros-noetic-rosserial-arduino
sudo apt-get install ros-noetic-rosserial
```
Go to ~/Desktop/Arduino/libraries directory and remove ros_lib folder. From this directory execute:
```shell
rosrun rosserial_arduino make_libraries.py .
```
### **2.7. Install ROS Noetic**
Open web browser in: http://wiki.ros.org/noetic/Installation/Ubuntu

## **3. Install drivers**
You will need to install:
- rplidar
- usbcam

First step is:
- Setup your computer to accept software from packages.ros.org.
```shell
sudo sh -c 'echo "deb http://packages.ros.org/ros/ubuntu $(lsb_release -sc) main" > /etc/apt/sources.list.d/ros-latest.list'
sudo apt update
sudo apt upgrade
```

### **3.1. Install rplidar**
You need to install the package: http://wiki.ros.org/rplidar

```shell
sudo apt install ros-noetic-rplidar-ros
```

### **3.2. Install usb-cam**
You need to install the package: https://wiki.ros.org/usb_cam

```shell
sudo apt install ros-noetic-usb-cam
```
You need to test which video device is connected and change it on the launch file (usb_cam_rock.launch)

### **3.3. Install Rosserial**
You need to install the package: http://wiki.ros.org/rosserial

```shell
sudo apt-get install ros-noetic-rosserial
```

## **4. rUBot mecanum bringup**
You can bringup your robot with:
```shell
roslaunch rubot_mecanum_description rubot_bringup_hw_rock.launch
```
You are ready to work with

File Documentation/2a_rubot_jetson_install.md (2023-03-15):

# **rUBot mecanum in Jetson-nano Install**

The main objectives are:
- Setup the Jetson nano 
- Add init with Hotspot
- Install Nomachine remote desktop
- Update to ubuntu20.04
- Install ROS Noetic
- Clone and sync a repository

We can finf this board in 2 versions:
- J1010 NVIDIA Jetson Nano, CPU ARM, GPU Maxwell, 4GB RAM, 16GB eMMc: https://es.farnell.com/seeed-studio/110061362/placa-portadora-nvidia-jetson/dp/4126473?MER=sy-me-pd-mi-acce
- J2021 NVIDIA Jetson Nano, CPU ARM, GPU Maxwell, 8GB RAM, 16GB eMMc: https://es.farnell.com/seeed-studio/110061381/kit-des-nvidia-jetson-xavier-nx/dp/4126474?MER=sy-me-pd-mi-acce

References:
- https://www.seeedstudio.com/Jetson-10-1-A0-p-5336.html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
- https://github.com/dusty-nv/jetson-inference
- https://developer.nvidia.com/embedded/learn/get-started-jetson-nano-devkit#intro

## **1. Setup the Jetson nano**

For the first time, let's follow the instructions in: https://wiki.seeedstudio.com/J1010_Boot_From_SD_Card/

Follow instructions to:
- Format a new 64GB SD card
- Download a Jetson nano Image
- Copy the image to the formatted SD Card using Balena Etcher
- Place the SD Card on the proper slot and Power on the Board

Some configurations will be needed:
- User name: mpuig
- Password: ubuntu1234

Your system is ready but you need to connect an external screen, keyboard and mouse. 

Our next objective is to enable a remote connection from another computer.
## **2. Add init with Hotspot**

For remote connection we need the Jetson-nano board to start in hotspot mode. To install this performance, follow the instructions:
- Plug a dongle USB: tp-link AC600 Nano Wireless USB Adapter Archer T2U Nano
- Select "System settings" and "Network" and "Wireless"
- Select "Use as Hotspot" and turn on.
- Select "Network connections" from top menu and edit the wi-fi hotspot
- Change the mode to "Hotspot"
- Change the SSID name to "rUBot_01" for exemple
- You can change the password key in:
  - /etc/NetworkManager/system-connections/Hotspot
  - or in terminal type:
  ```shell
  nm-connection-editor
  ```
- Restart the network manager
```shell
sudo systemctl restart NetworkManager
```
- reboot the board to start the board with hotspot
- From another computer you can see this network and you can connect to it.

To select this Hotspot automatically on restart:
- open a terminal and see all the connection names:
  ```shell
  nmcli con show
  ```
- Make the connection "Hotspot" start automatically:
  ```shell
  nmcli con mod Hotspot connection.autoconnect yes
  ``` 
- Verify listing all the Hotspot parameters including "autoconnect"
  ```shell
  nmcli con show Hotspot
  ```
## **3. Install Nomachine remote desktop and setup**
For a remote connection, download and install nomachine in PC and Board:
- In Jetson nano Board, download Nomachine for ARMv8 DEB: https://downloads.nomachine.com/download/?id=114&distro=ARM
- In PC, download Nomachine for windows 64bits: https://downloads.nomachine.com/download/?id=8

**Setup**

The raspberrypi4 is configured:
- to generate a hotspot "rUBot_xx"
- NoMachine activated 

When powering the Jetson Nano, generates a hotspot you have to connect to:
- SSID name: rUBot_01 
- password "25d5e74416"

Once you are connected to this network you will be able to connect your computer to the Jetson Nano using NoMachine viewer:
- In PC open NoMachine viewer
- Select the Jetson Nano IP address: 10.42.0.1
- you have to specify:
    - user: mpuig
    - password: ubuntu1234
- You will have the Jetson Nano desktop on your windows NoMachine screen

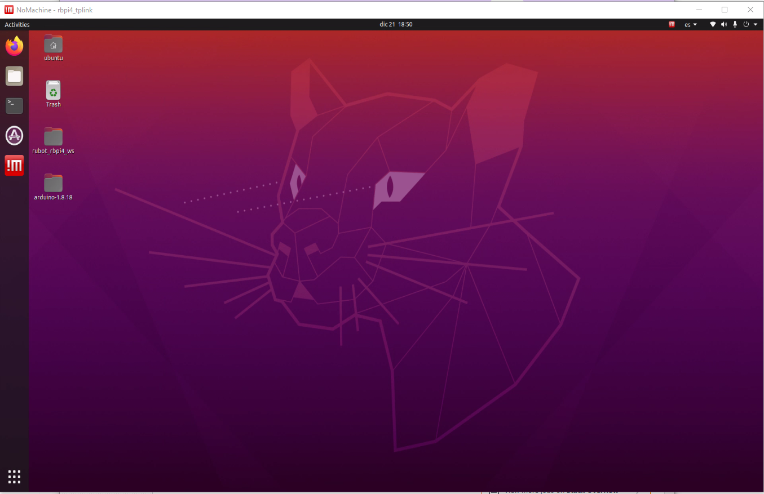
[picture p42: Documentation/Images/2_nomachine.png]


If you want to change the Hotspot name (one for each robot):
- Change the Hotspot settings (name or password):
```shell
sudo nm-connection-editor
```
- Identify the IP of the rbpi4 Hotspot:
  - type ifconfig
  - in wlan0 you identify the inet address: 10.42.0.1

## **4. Update to ubuntu20.04**

The Jetson nano J1010 board is preinstalled with Ubuntu 18 

- First update and upgrade the ubuntu version:
```shell
sudo apt update
sudo apt upgrade
sudo apt update
```
- Reboot and Open "software updater" and update the actual version and empty the waste
- Open a terminal and type:
```shell
sudo do-release-upgrade
```
- Select the Ubuntu20.04 to work with ROS Noetic

Follow the steps in order to properly install the Raspberrypi:

### **2.2. ROS Noetic Desktop installation**

Follow the instructions on: http://wiki.ros.org/noetic/Installation/Ubuntu
> Is recommended to update and upgrade first:
```shell
sudo apt update
sudo apt upgrade
sudo apt update
```
### **2.3. Create WiFi Hotspot and setup**

Follow instructions in: https://www.debugpoint.com/2020/04/how-to-create-wifi-hotspot-in-ubuntu-20-04-lts/

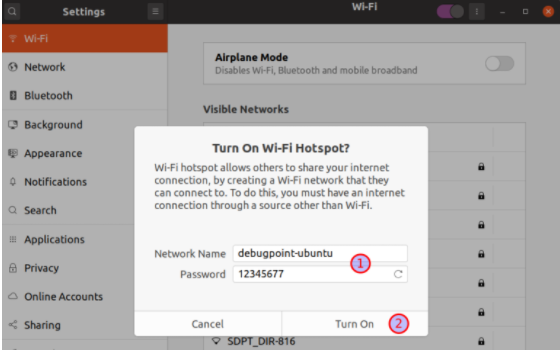
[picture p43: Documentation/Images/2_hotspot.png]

>Carefull!:
>- If "Turn On Wi-Fi Hotspot is disabled select another setting (i.e. Bluetooth) and come back to Wi-Fi setting
>- Choose a SSID corresponding to your robot name

To select this Hotspot automatically on restart:
- open a terminal and see all the connection names:
```shell
nmcli con show
```
- Make the connection "Hotspot" start automatically:
```shell
nmcli con mod Hotspot connection.autoconnect yes
``` 
- Verify listing all the Hotspot parameters including "autoconnect"
```shell
nmcli con show Hotspot
```

### **2.4. Create your workspace**

We will create the workspace where we will install all needed packages for our Hardware project
```shell
mkdir -p ~/Desktop/rubot_rbpi4_ws/src
cd ~/Desktop/rubot_rbpi4_ws/
catkin_make
echo "source ~/Desktop/rubot_rbpi4_ws/devel/setup.bash" >> ~/.bashrc
```
We will install:
- Raspberrypi camera
- rpLIDAR
- Arduino board with rosserial
### **Install raspberrypi camera**
Information is located on: https://picamera.readthedocs.io/en/release-1.11/install.html

You need to activate the raspicam in Ubuntu:
- open the file config.txt
```shell
sudo nano /boot/firmware/config.txt
```
- add the magic line start_x=1 at the end
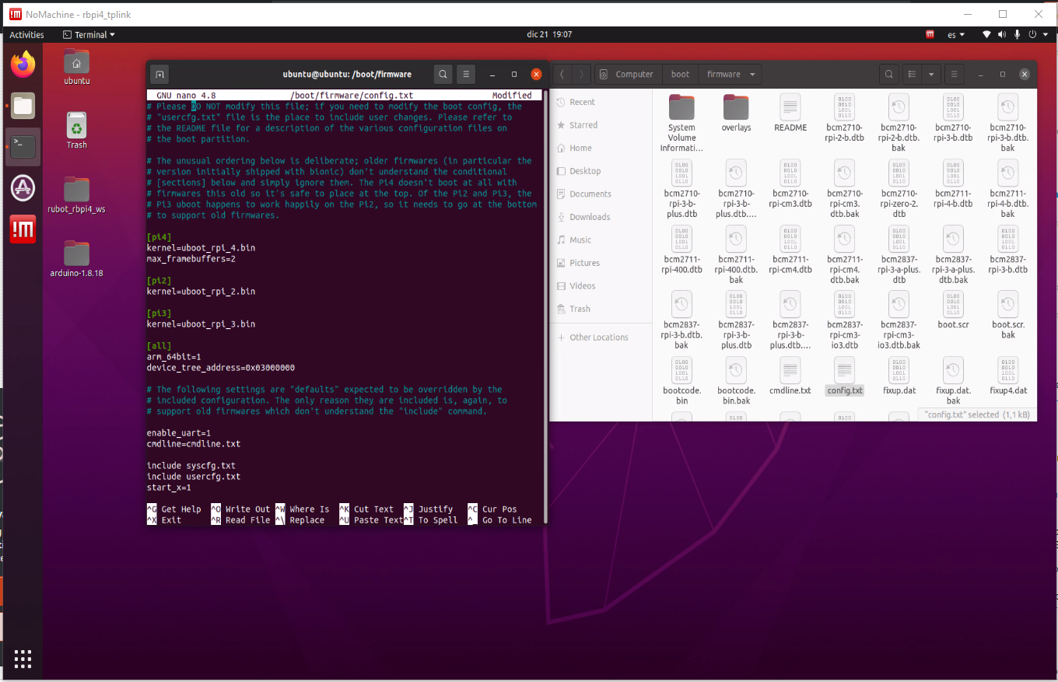
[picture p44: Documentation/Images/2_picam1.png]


- reboot
- update your system to install the necessary drivers:
```shell
sudo apt update
sudo apt upgrade
```
Now we will install the python module for picamera:
```shell
sudo apt install python3-pip
pip install picamera
```
And the needed libraries for raspicam package:
```shell
sudo apt-get install -y libyaml-cpp-dev
sudo apt-get install -y libogg-dev libvorbis-dev libtheora-dev
```
Finally to work with raspicam in ROS, you need to install the packages:
```shell
git clone https://github.com/UbiquityRobotics/raspicam_node.git
git clone --single-branch --branch=noetic-devel https://github.com/ros-perception/image_transport_plugins.git
git clone --single-branch --branch=noetic https://github.com/ros-perception/vision_opencv.git
git clone --single-branch --branch=noetic-devel https://github.com/ros-perception/image_common.git
```
> Follow the Build instructions in: https://github.com/UbiquityRobotics/raspicam_node.

> Make sure that your user is in the video group by running groups|grep video 
```shell
sudo usermod -a -G video ubuntu
```

Then you are able to compile the workspace:
```shell
cd ~/Desktop/rubot_rbpi4_ws/
catkin_make
```

### **Install rpLIDAR**

Open a terminal in src folder and type:
```shell
cd ~/Desktop/rubot_rbpi4_ws/src
git clone https://github.com/Slamtec/rplidar_ros
cd ..
catkin_make
```
To test the sensor, connect the LIDAR sensor to RB Pi and execute:
```shell
roslaunch rplidar_ros view_rplidar.launch
```
### **Install ARDUINO**

This robot will be controlled by an Arduino Mega board.

The arduino program will start a serial_node with all the topics

The Arduino programm is located in "files/Arduino_node" folder.

Considering your Raspberry computer uses Ubuntu 20, as explained in previous sections, you need to download Arduino IDE version for Linux ARM 64 bits from the following link: https://www.arduino.cc/en/software.

After dowloading the zip file, reclocate it and unzip it in the Tools folder: ~/Tools/Arduino-1.8.18. From this directory, open a terminal and execute the following commands:

```shell
sudo ./install.sh
cd ~
gedit .bashrc
export PATH=$PATH:$HOME/Desktop/Arduino-1.8.18
```
Save and close the file and install rosserial for ROS Noetic using:
```shell
sudo apt-get install ros-noetic-rosserial-arduino
sudo apt-get install ros-noetic-rosserial
```
Go to ~/Desktop/Arduino-1.8.18/libraries directory and remove ros_lib folder. From this directory execute:
```shell
rosrun rosserial_arduino make_libraries.py .
```

Test Arduino ROS library with "Hello World" exemple: http://wiki.ros.org/rosserial_arduino/Tutorials/Hello%20World

### **Manage USB ports**

The rbpi4 manage arduino board and rpLIDAR with 2 USB ports. 

We have to force the same USB port to the same device:
- "arduino" port to arduino mega board
- "rplidar" port to rpLIDAR

This can be done creating UDEV rules for each devide:

**a) Arduino udev rules**

Follow instructions: 
- https://steve.fi/hardware/arduino-basics/
- https://medium.com/@darshankt/setting-up-the-udev-rules-for-connecting-multiple-external-devices-through-usb-in-linux-28c110cf9251

  Connect the Arduino Mega in USB port. To see the port name type:
  ```shell
  ls -l /dev/ttyAMC*
  ```
  Give permissions rwx to this port ttyACM*
  ```shell
  sudo chmod 777 /dev/ttyACM*
  ```
  To see the needed properties to create udev rules, type:
  ```shell
  lsusb
  ```
  You will see:
  ```shell
  ubuntu@ubuntu:/usr/lib/udev/rules.d$ lsusb
  Bus 002 Device 001: ID 1d6b:0003 Linux Foundation 3.0 root hub
  Bus 001 Device 007: ID 2341:0042 Arduino SA Mega 2560 R3 (CDC ACM)
  Bus 001 Device 004: ID 0e8f:00fb GreenAsia Inc. 
  Bus 001 Device 003: ID 04d9:a01c Holtek Semiconductor, Inc. wireless multimedia keyboard with trackball [Trust ADURA 17911]
  Bus 001 Device 002: ID 2109:3431 VIA Labs, Inc. Hub
  Bus 001 Device 001: ID 1d6b:0002 Linux Foundation 2.0 root hub
  ```
  The create a file /etc/udev/rules.d/99-arduino.rules and give it the following contents:
  ```xml
  # Arduino port definition
  SUBSYSTEM=="tty", GROUP="plugdev", MODE="0660"

  ACTION=="add", SUBSYSTEMS=="usb", ATTRS{idVendor}=="2341", ATTRS{idProduct}=="0042", SYMLINK+="arduino"
  ```
  >The idProduct and idVendor corresponds to the numbers in the Arduino line.

  Now restart the service:
  ```shell
  sudo /etc/init.d/udev restart 
  ```
  Unplug and plug again the Arduino Board and verify if the symlink is created:
  ```shell
  ls -l /dev/arduino /dev/ttyACM0
  ```
  If all is OK, you will see:
  ```shell
  lrwxrwxrwx 1 root root         7 dic 23 08:58 /dev/arduino -> ttyACM0
  crw-rw---- 1 root plugdev 166, 0 dic 23 08:58 /dev/ttyACM0
  ```

**b) rpLIDAR udev rules**

Follow instructions:  
- https://github.com/Slamtec/rplidar_ros/tree/master/scripts

  Connect the rpLIDAR in USB port. To see the port name type:
  ```shell
  ls -l /dev/ttyUSB*
  ```
  Give permissions rwx to this port ttyUSB*
  ```shell
  sudo chmod 777 /dev/ttyACM*
  ```
  To see the needed properties to create udev rules, type:
  ```shell
  lsusb
  ```
  You will see your rpLIDAR device properties:
  ```shell
  Bus 001 Device 010: ID 10c4:ea60 Silicon Labs CP210x UART Bridge
  ```
  The create a file /etc/udev/rules.d/rplidar.rules and give it the following contents:
  ```xml
  # set the udev rule , make the device_port be fixed by rplidar
  #
  KERNEL=="ttyUSB*", ATTRS{idVendor}=="10c4", ATTRS{idProduct}=="ea60", MODE:="0777", SYMLINK+="rplidar"
  ```
  Now restart the service:
  ```shell
  sudo /etc/init.d/udev restart 
  ```
  Unplug and plug again the Arduino Board and verify if the symlink is created:
  ```shell
  ls -l /dev/arduino /dev/ttyACM0 /dev/rplidar /dev/ttyUSB0
  ```
  If all is OK, you will see:
  ```shell
  lrwxrwxrwx 1 root root         7 dic 23 09:31 /dev/arduino -> ttyACM0
  lrwxrwxrwx 1 root root         7 dic 23 09:31 /dev/rplidar -> ttyUSB0
  crw-rw---- 1 root plugdev 166, 0 dic 23 09:31 /dev/ttyACM0
  crwxrwxrwx 1 root plugdev 188, 0 dic 23 09:31 /dev/ttyUSB0
  ```

You have now your rUBot_mecanum ready to work-with!!

### **Install joy control**

Almost all robots subscribe /cmd_vel topic whose message type is Twist for controlling robots.

#### **PS2 device**
Follow the steps:
- Connect the USB to the rbp4 and push start
- review the new device associated to the ps2
```shell
dmesg -w
```
- identify the assigned input. In raspberryPi4 appears dev/input/js0. In rock4 appears dev/hidraw1
- change mod to "rwxrwxrw-" in dev/input/js0
```shell
sudo chmod a+rw dev/input/js0
```
- install gstest-gtk
```shell
sudo apt install gstest-gtk
```
- Install teleop-twist-joy
```shell
sudo apt install ros-noetic-teleop-twist-joy
```
- create a config folder in src and place inside the "ps3-holonomic.config.yaml" file from teleop-twist-joy package. Configure the button position as desired
- copy the teleop.launch file from teleop-twist-joy package to launch folder of rubot_control package. Change the config folder location in the specific parameter
- run
```shell
roslaunch teleop_twist_joy teleop.launch
```

Test the /joy and /cmd_vel topic's contents

### **Copy the final work-space**

The best way is to copy a zip file of the final work-space (including the build and devel folders) in a pen drive and copy it to each raspberrypi robot.

Usually the file properties are lost and in the ws folder you have to make all files executable:
```shell
cd ~/Desktop/rUBot_mecanum_ws
sudo chmod -R +x ./*
```
You will have the ws ready to work with!

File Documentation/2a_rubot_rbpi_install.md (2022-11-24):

# **rUBot mecanum in Raspberrypi4 Setup&Control**

The main objectives are:
- Assemble a real robot (rUBot mecanum)
- Setup the HW drivers in raspberrypi4
- Control the rUBot movement

Let's see how to fulfill these objectives

References:
- https://github.com/ros-mobile-robots/diffbot
- https://johanschwind.medium.com/mobile-robot-teleoperation-with-the-jetson-nano-and-ros-d72b4b57e9be

## **1. rUBot assembling**

This tobot prototype is based on:
- Mecanum wheel chasis:
  - https://es.aliexpress.com/item/4001121790912.html?gatewayAdapt=glo2esp&spm=a2g0o.9042311.0.0.3c7963c0XKupJW
- Battery 12V&5V (3Ah):
  - https://www.amazon.es/gp/product/B072HR211P/ref=ppx_yo_dt_b_asin_title_o05_s00?ie=UTF8&psc=1
- Battery 12V (6,7 and 20Ah): 
  - https://www.amazon.es/gp/product/6040388099/ref=ewc_pr_img_1?smid=A17M1OH9UAKGE7&psc=1
  - https://www.amazon.es/gp/product/B07YSCXGNF/ref=ppx_yo_dt_b_asin_title_o07_s00?ie=UTF8&psc=1
  - https://www.amazon.es/THENAGD-Recargable-Interruptor-Encendido-DC-122000/dp/B091F465RP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
- Battery 12V/5V
  - https://www.amazon.es/gp/product/B072HR211P/ref=ppx_yo_dt_b_asin_title_o05_s00?ie=UTF8&psc=1
  - https://www.amazon.es/gp/product/6040387874/ref=ox_sc_act_title_1?smid=A17M1OH9UAKGE7&psc=1 
- Battery 5V (20 and 26Ah):
  - https://www.amazon.es/dp/B09MYQFXP5?psc=1&smid=AKVUAZL0K2E1J&ref_=chk_typ_imgToDp
  - https://www.amazon.es/SWEYE-Capacidad%EF%BC%BDCargador-M%C3%BAltiples-Protecciones-Smartphones/dp/B0814JMRLR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
- On-board Raspberrypi4
  - https://es.rs-online.com/web/p/raspberry-pi/2012367
  - https://es.rs-online.com/web/p/placas-hat-y-complementos-para-raspberry-pi/2208633
- Arduino mega: for HW driver control
  - https://es.rs-online.com/web/p/arduino/7154084
- Arduino motor driver shield TB6612FNG:
  - https://es.aliexpress.com/item/4001086592215.html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
  - https://github.com/Seeed-Studio/Grove_Motor_Driver_TB6612FNG
- RaspiCAM RGB camera:
  - https://es.rs-online.com/web/p/camaras-para-raspberry-pi/9132664
  - https://es.rs-online.com/web/p/cajas-para-raspberry-pi/8679049
- rpLidar:
  - https://www.robotshop.com/es/es/rplidar-a1m8-kit-desarrollo-escaner-laser-360-grados.html
- USB cables:
  - USB-A to USB-B: https://www.amazon.es/gp/product/B073XQ33L2/ref=ppx_yo_dt_b_asin_title_o01_s00?ie=UTF8&th=1
  - USB-C to USB-B: https://www.amazon.es/gp/product/B08RXQJJ9Z/ref=ppx_yo_dt_b_asin_title_o02_s00?ie=UTF8&th=1
  - microUSB to USB-B: https://www.amazon.es/gp/product/B00WMAQKS2/ref=ppx_yo_dt_b_asin_title_o04_s00?ie=UTF8&th=1

Getting Started

Other platforms:
- https://www.superdroidrobots.com/robotic-kits-platforms/mecanum-robots
- https://www.robotshop.com/es/es/kit-robot-arduino-con-rueda-mecanum-4wd-60-mm.html
- https://www.robotshop.com/es/es/4wd-robot-basico-mecanum-compatible-con-arduino.html

## **2. Setup the HW drivers in raspberrypi4**
The raspberrypi4 onboard is preinstalled with:
- Ubuntu 20 server 64bits
  - NoMachine remote desktop
- ROS Noetic
- rubot_rbpi4_ws repository is located in /home/pi/Desktop folder 

### **2.1. Install Ubuntu 20 server 64bits**

Follow the steps in order to properly install the Raspberrypi:

- Install Raspberry Pi OS using Raspberry Pi Imager (download for windows): https://www.raspberrypi.org/software/
- Run the application and save the image:
  - Ubuntu --> Ubuntu 20 server 64bits to the SD card
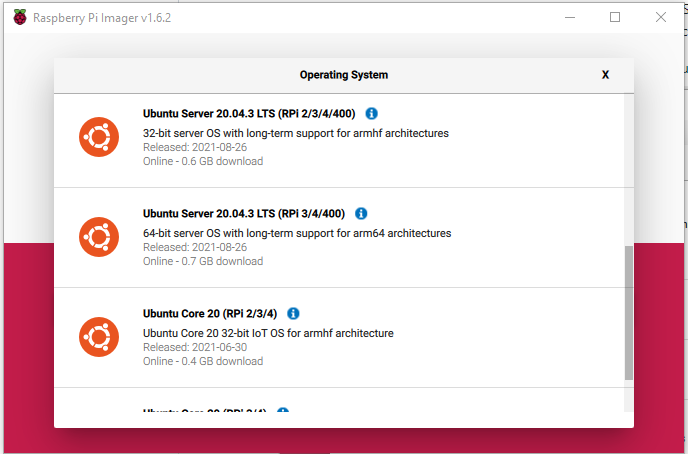
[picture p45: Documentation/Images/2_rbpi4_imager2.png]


- Insert the SD in a RBPi board and connect it to screen and ethernet cable to the router
- power the raspberrypi4 and login:
  - login: ubuntu
  - password: ubuntu
- You will have to change the password (we use ubuntu1234)
> Note: 
> - Connect HDMI just after power rbpi4
> - Keyboard is not ESP and "-" is on "'" key

**Install Ubuntu Desktop**

In the terminal, type:
```shell
sudo apt-get install ubuntu-desktop
```
> Follow instructions:
>- Perhaps you may type "sudo dpkg --configure -a"

After some minutes, the desktop is installed. 
> You have to update and upgrade the ubuntu now (type it several times untill all packages will be updated)

Type:
```shell
reboot
```
You will get the ubuntu 20 desktop

- choose a wifi network and change the timezone, language and password

**Install nomachine remote desktop**

Download nomachine in RaspberryPi and PC:
- In raspberryPi:
  - Download the Raspberrypy4 version ARMv8 DEB in: https://www.nomachine.com/download/linux&id=29&s=Raspberry
  - open a terminal in download folder and install following the instructions
- In PC: https://www.nomachine.com/

**Notebook visualization in raspberrypi**

Use the NBviewer program from Jupyter:

https://nbviewer.ipython.org/

### **2.2. ROS Noetic Desktop installation**

Follow the instructions on: http://wiki.ros.org/noetic/Installation/Ubuntu
> Is recommended to update and upgrade first:
```shell
sudo apt update
sudo apt upgrade
sudo apt update
```
### **2.3. Create WiFi Hotspot and setup**

Follow instructions in: https://www.debugpoint.com/2020/04/how-to-create-wifi-hotspot-in-ubuntu-20-04-lts/


>Carefull!:
>- If "Turn On Wi-Fi Hotspot is disabled select another setting (i.e. Bluetooth) and come back to Wi-Fi setting
>- Choose a SSID corresponding to your robot name

To select this Hotspot automatically on restart:
- open a terminal and see all the connection names:
```shell
nmcli con show
```
- Make the connection "Hotspot" start automatically:
```shell
nmcli con mod Hotspot connection.autoconnect yes
``` 
- Verify listing all the Hotspot parameters including "autoconnect"
```shell
nmcli con show Hotspot
```
- Identify the IP of the rbpi4 Hotspot:
  - type ifconfig
  - in wlan0 you identify the inet address: 10.42.0.1

**Setup**

The raspberrypi4 is configured:
- to generate a hotspot "rUBot_xx"
- NoMachine activated 
- raspicam activated 

When powering the raspberrypi4, generates a hotspot you have to connect to:
- SSID name: rUBot_01 
- password "rUBot_Mec"

Once you are connected to this network you will be able to connect your computer to the raspberrypi4 using NoMachine viewer:
- In PC open NoMachine viewer
- Select the raspberrypi IP address: 10.42.0.1
- you have to specify:
    - user: ubuntu
    - password: ubuntu1234
- You will have the raspberrypi4 desktop on your windows NoMachine screen



If you want to change the Hotspot name (one for each robot):
- Change the Hotspot settings (name or password):
```shell
sudo nm-connection-editor
```

### **2.4. Create your workspace**

We will create the workspace where we will install all needed packages for our Hardware project
```shell
mkdir -p ~/Desktop/rubot_rbpi4_ws/src
cd ~/Desktop/rubot_rbpi4_ws/
catkin_make
echo "source ~/Desktop/rubot_rbpi4_ws/devel/setup.bash" >> ~/.bashrc
```
We will install:
- Raspberrypi camera
- rpLIDAR
- Arduino board with rosserial
### **Install raspberrypi camera**
Information is located on: https://picamera.readthedocs.io/en/release-1.11/install.html

You need to activate the raspicam in Ubuntu:
- open the file config.txt
```shell
sudo nano /boot/firmware/config.txt
```
- add the magic line start_x=1 at the end


- reboot
- update your system to install the necessary drivers:
```shell
sudo apt update
sudo apt upgrade
```
Now we will install the python module for picamera:
```shell
sudo apt install python3-pip
pip install picamera
```
And the needed libraries for raspicam package:
```shell
sudo apt-get install -y libyaml-cpp-dev
sudo apt-get install -y libogg-dev libvorbis-dev libtheora-dev
```
Finally to work with raspicam in ROS, you need to install the packages:
```shell
git clone https://github.com/UbiquityRobotics/raspicam_node.git
git clone --single-branch --branch=noetic-devel https://github.com/ros-perception/image_transport_plugins.git
git clone --single-branch --branch=noetic https://github.com/ros-perception/vision_opencv.git
git clone --single-branch --branch=noetic-devel https://github.com/ros-perception/image_common.git
```
> Follow the Build instructions in: https://github.com/UbiquityRobotics/raspicam_node.

> Make sure that your user is in the video group by running groups|grep video 
```shell
sudo usermod -a -G video ubuntu
```

Then you are able to compile the workspace:
```shell
cd ~/Desktop/rubot_rbpi4_ws/
catkin_make
```

### **Install rpLIDAR**

Open a terminal in src folder and type:
```shell
cd ~/Desktop/rubot_rbpi4_ws/src
git clone https://github.com/Slamtec/rplidar_ros
cd ..
catkin_make
```
To test the sensor, connect the LIDAR sensor to RB Pi and execute:
```shell
roslaunch rplidar_ros view_rplidar.launch
```
### **Install ARDUINO**

This robot will be controlled by an Arduino Mega board.

The arduino program will start a serial_node with all the topics

The Arduino programm is located in "files/Arduino_node" folder.

Considering your Raspberry computer uses Ubuntu 20, as explained in previous sections, you need to download Arduino IDE version for Linux ARM 64 bits from the following link: https://www.arduino.cc/en/software.

After dowloading the zip file, reclocate it and unzip it in the Tools folder: ~/Tools/Arduino-1.8.18. From this directory, open a terminal and execute the following commands:

```shell
sudo ./install.sh
cd ~
gedit .bashrc
export PATH=$PATH:$HOME/Desktop/Arduino-1.8.18
```
Save and close the file and install rosserial for ROS Noetic using:
```shell
sudo apt-get install ros-noetic-rosserial-arduino
sudo apt-get install ros-noetic-rosserial
```
Go to ~/Desktop/Arduino-1.8.18/libraries directory and remove ros_lib folder. From this directory execute:
```shell
rosrun rosserial_arduino make_libraries.py .
```

Test Arduino ROS library with "Hello World" exemple: http://wiki.ros.org/rosserial_arduino/Tutorials/Hello%20World

### **Manage USB ports**

The rbpi4 manage arduino board and rpLIDAR with 2 USB ports. 

We have to force the same USB port to the same device:
- "arduino" port to arduino mega board
- "rplidar" port to rpLIDAR

This can be done creating UDEV rules for each devide:

**a) Arduino udev rules**

Follow instructions: 
- https://steve.fi/hardware/arduino-basics/
- https://medium.com/@darshankt/setting-up-the-udev-rules-for-connecting-multiple-external-devices-through-usb-in-linux-28c110cf9251

  Connect the Arduino Mega in USB port. To see the port name type:
  ```shell
  ls -l /dev/ttyAMC*
  ```
  Give permissions rwx to this port ttyACM*
  ```shell
  sudo chmod 777 /dev/ttyACM*
  ```
  To see the needed properties to create udev rules, type:
  ```shell
  lsusb
  ```
  You will see:
  ```shell
  ubuntu@ubuntu:/usr/lib/udev/rules.d$ lsusb
  Bus 002 Device 001: ID 1d6b:0003 Linux Foundation 3.0 root hub
  Bus 001 Device 007: ID 2341:0042 Arduino SA Mega 2560 R3 (CDC ACM)
  Bus 001 Device 004: ID 0e8f:00fb GreenAsia Inc. 
  Bus 001 Device 003: ID 04d9:a01c Holtek Semiconductor, Inc. wireless multimedia keyboard with trackball [Trust ADURA 17911]
  Bus 001 Device 002: ID 2109:3431 VIA Labs, Inc. Hub
  Bus 001 Device 001: ID 1d6b:0002 Linux Foundation 2.0 root hub
  ```
  The create a file /etc/udev/rules.d/99-arduino.rules and give it the following contents:
  ```xml
  # Arduino port definition
  SUBSYSTEM=="tty", GROUP="plugdev", MODE="0660"

  ACTION=="add", SUBSYSTEMS=="usb", ATTRS{idVendor}=="2341", ATTRS{idProduct}=="0042", SYMLINK+="arduino"
  ```
  >The idProduct and idVendor corresponds to the numbers in the Arduino line.

  Now restart the service:
  ```shell
  sudo /etc/init.d/udev restart 
  ```
  Unplug and plug again the Arduino Board and verify if the symlink is created:
  ```shell
  ls -l /dev/arduino /dev/ttyACM0
  ```
  If all is OK, you will see:
  ```shell
  lrwxrwxrwx 1 root root         7 dic 23 08:58 /dev/arduino -> ttyACM0
  crw-rw---- 1 root plugdev 166, 0 dic 23 08:58 /dev/ttyACM0
  ```

**b) rpLIDAR udev rules**

Follow instructions:  
- https://github.com/Slamtec/rplidar_ros/tree/master/scripts

  Connect the rpLIDAR in USB port. To see the port name type:
  ```shell
  ls -l /dev/ttyUSB*
  ```
  Give permissions rwx to this port ttyUSB*
  ```shell
  sudo chmod 777 /dev/ttyACM*
  ```
  To see the needed properties to create udev rules, type:
  ```shell
  lsusb
  ```
  You will see your rpLIDAR device properties:
  ```shell
  Bus 001 Device 010: ID 10c4:ea60 Silicon Labs CP210x UART Bridge
  ```
  The create a file /etc/udev/rules.d/rplidar.rules and give it the following contents:
  ```xml
  # set the udev rule , make the device_port be fixed by rplidar
  #
  KERNEL=="ttyUSB*", ATTRS{idVendor}=="10c4", ATTRS{idProduct}=="ea60", MODE:="0777", SYMLINK+="rplidar"
  ```
  Now restart the service:
  ```shell
  sudo /etc/init.d/udev restart 
  ```
  Unplug and plug again the Arduino Board and verify if the symlink is created:
  ```shell
  ls -l /dev/arduino /dev/ttyACM0 /dev/rplidar /dev/ttyUSB0
  ```
  If all is OK, you will see:
  ```shell
  lrwxrwxrwx 1 root root         7 dic 23 09:31 /dev/arduino -> ttyACM0
  lrwxrwxrwx 1 root root         7 dic 23 09:31 /dev/rplidar -> ttyUSB0
  crw-rw---- 1 root plugdev 166, 0 dic 23 09:31 /dev/ttyACM0
  crwxrwxrwx 1 root plugdev 188, 0 dic 23 09:31 /dev/ttyUSB0
  ```

You have now your rUBot_mecanum ready to work-with!!

### **Install joy control**

Almost all robots subscribe /cmd_vel topic whose message type is Twist for controlling robots.

#### **PS2 device**
Follow the steps:
- Connect the USB to the rbp4 and push start
- review the new device associated to the ps2
```shell
dmesg -w
```
- identify the assigned input. In raspberryPi4 appears dev/input/js0. In rock4 appears dev/hidraw1
- change mod to "rwxrwxrw-" in dev/input/js0
```shell
sudo chmod a+rw dev/input/js0
```
- install gstest-gtk
```shell
sudo apt install gstest-gtk
```
- Install teleop-twist-joy
```shell
sudo apt install ros-noetic-teleop-twist-joy
```
- create a config folder in src and place inside the "ps3-holonomic.config.yaml" file from teleop-twist-joy package. Configure the button position as desired
- copy the teleop.launch file from teleop-twist-joy package to launch folder of rubot_control package. Change the config folder location in the specific parameter
- run
```shell
roslaunch teleop_twist_joy teleop.launch
```

Test the /joy and /cmd_vel topic's contents

### **Copy the final work-space**

The best way is to copy a zip file of the final work-space (including the build and devel folders) in a pen drive and copy it to each raspberrypi robot.

Usually the file properties are lost and in the ws folder you have to make all files executable:
```shell
cd ~/Desktop/rUBot_mecanum_ws
sudo chmod -R +x ./*
```
You will have the ws ready to work with!

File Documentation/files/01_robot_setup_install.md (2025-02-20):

# **ROBOTsetup**

The objectives are:

- Configure the raspberrypi
- Install and bringup the robot model

We will use a raspberrypi4 board with ubuntu20 ROS Noetic and a hotspot wifi connection.

## **1. Configure the raspberrypi**

We will use a raspberrypi4 board with ubuntu20 ROS Noetic intalled.

There are 2 different options for this installation:

- Install ubuntu20 server image and ROS Noetic
- Install Raspberrypi Desktop and ROS Noetic with Docker

### **1.1. Install Ubuntu20 server image**

Follow the steps in order to properly install the Ubuntu20 on Raspberrypi:

- Run Raspberry Pi Imager (https://www.raspberrypi.org/software/)
  - select Device: Raspberrypi4
  - select OS Ubuntu --> Ubuntu 20 server 64bits to the SD card
  - Select the configurations:
    - Name: rUBotxx
    - User: ubuntu
    - Pass: ubuntu1234
    - LAN config: wifi you want to connect (i.e. rUBotics)
    - Regional settings: ES
    - Services: activate ssh
- Insert the SD in a RBPi board and connect it to screen and ethernet cable to the router
- power the raspberrypi4 and login:
  - login: ubuntu
  - password: ubuntu1234
- update the OS:
  ````shell
  sudo apt update
  sudo apt upgrade
  sudo reboot
  ````
- If you want to change the hostname later:
  ````shell
  sudo hostnamectl set-hostname nou_hostname
  sudo reboot
  ````

If you want to create other **wifi connections and a Hotspot**.

- Install ubuntu Desktop:
  ````shell
  sudo apt install ubuntu-desktop
  sudo reboot
  ````
  > this will take 10 minutes and you have to select "gdm3" during process

- In Ubuntu Desktop graphical interface, create a **Hotspot** following instructions in: https://www.debugpoint.com/2020/04/how-to-create-wifi-hotspot-in-ubuntu-20-04-lts/

  - Select Wi-Fi settings
  - Select "Turn On Wi-Fi Hotspot"
    >Carefull!:
    >- If "Turn On Wi-Fi Hotspot" is disabled select another setting (i.e. Bluetooth) and come back to Wi-Fi setting
  - Choose a SSID corresponding to your robot name
    - Name: rubot_01
    - Pass: rUBot_Mec
  - To change the Hotspot settings (name or password):
    ```shell
    sudo nm-connection-editor
    ```
- To create other **wifi networks**, use the Desktop graphical interface to easy select the available wifi and configure to start automatically with priorities (higher number corresponds to higher priority)
  >Review the default wifi network defined on the Ubuntu20 image creation with "Imager"
- If you want to use the robot Hotspot within Nomachine remote desktop, you will have to install Nomachine in raspberypi: https://downloads.nomachine.com/es/download/?id=106&distro=Raspberry&hw=Pi4
- If you want to configure a fixed IP:
    - "sudo nm-connection-editor"
    - Select the "Robotics_UB" wifi connection
    - In section "IPv4 settings" Select "Manual"
    - Add IP address and choose the desired IP (192.168.0.61), Netmask (255.255.255.0), Gateway (192.168.0.1)
    - Add DNS server (8.8.8.8) for google DNS
    - Apply and reboot

### **1.2. Install ROS Noetic Desktop**

Follow the instructions on: http://wiki.ros.org/noetic/Installation/Ubuntu
> Is recommended to update and upgrade first:
```shell
sudo apt update
sudo apt upgrade
```

### **1.3. Install Arduino**

Interesting review: https://www.clearpathrobotics.com/assets/guides/noetic/ros/Driving%20Husky%20with%20ROSSerial.html

- You need to install it with snap to be sure you have all dependencies. You can install Arduino IDE on Ubuntu and add your user to the dialout and tty groups:
  ````shell
  sudo snap install arduino
  sudo usermod -a -G tty ubuntu
  sudo usermod -a -G dialout ubuntu
  sudo reboot
  ````
- Install ROS Packages for Arduino:
  ````shell
  sudo apt install ros-noetic-rosserial
  sudo apt install ros-noetic-rosserial-arduino
  ````
- Install ROS Libraries:

  Go to the Arduino Sketchbook location and install libraries. With Arduino core you will surelly have to create the directory. If you have arduino programed, you will not need the ros_libraries:

  ````shell
  cd /home/ubuntu/snap/arduino/current/libraries/
  rosrun rosserial_arduino make_libraries.py .
  ````
  
  Restart your Arduino IDE and you should see the ros_lib part of your libraries!

### **1.4. Install rplidar**
You need to install the package: http://wiki.ros.org/rplidar

```shell
sudo apt install ros-noetic-rplidar-ros
```

### **1.5. Install usb-cam**
You need to install the package: https://wiki.ros.org/usb_cam

```shell
sudo apt install ros-noetic-usb-cam
```

### **1.6. Create the Service to bringup on boot**

It will be good to bringup the robot on boot:

- Create the script file:
  ````shell
  nano /home/ubuntu/start_rubot.sh
  ````
- Edit the script file:
  ````shell
  #!/bin/bash
  source /opt/ros/noetic/setup.bash
  source /home/ubuntu/rUBot_mecanum_ws/devel/setup.bash
  cd /home/ubuntu/rUBot_mecanum_ws
  roslaunch rubot_mecanum_description rubot_bringup_hw_arduino.launch
  ````
- Make the script executable:
  ````shell
  chmod +x /home/ubuntu/start_rubot.sh
  ````
- Create the service file:
  ````shell
  sudo nano /etc/systemd/system/rubot.service
  ````
- Edit the service file:
  ````shell
  [Unit]
  Description=Run robot bringup
  After=network.target

  [Service]
  ExecStart=/home/ubuntu/start_rubot.sh
  User=ubuntu
  Restart=always
  RestartSec=5
  Environment=HOME=/home/ubuntu
  WorkingDirectory=/home/ubuntu

  [Install]
  WantedBy=multi-user.target
  ````
- Reload systemd services:
  ````shell
  sudo systemctl daemon-reload
  ````
- Enable and start the service:
  ````shell
  sudo systemctl enable rubot.service
  sudo systemctl start rubot.service
  ````
**Test the Service**

- Check the status of the service:
  ````shell
  sudo systemctl status rubot.service
  sudo journalctl -u rubot.service -b
  ````
- Check ROS topics:
  ````shell
  rostopic list
  ````
**Modify the Service**

- Stop the servide:
  ````shell
  sudo systemctl stop rubot.service
  ````
- Make modifications in sh file or service file
- restart the service
  ````shell
  sudo systemctl daemon-reload
  sudo systemctl start rubot.service
  ````
> If the service was already enabled it is not needed to disable and enable again

**Remove the Service**
- Disable the service:
  ````shell
  sudo systemctl disable rubot.service
  ````
- Stop the service:
  ````shell
  sudo systemctl stop rubot.service
  ````
- Remove the service file:
  ````shell
  sudo rm /etc/systemd/system/rubot.service
  ````
- Reload systemd services:
  ````shell
  sudo systemctl daemon-reload
  ````

## **2. Configure Raspberrypi with Docker**

To create a fast and robust image of ROS Noetic for our robot, an improved method is to use Docker.

References:
- Docker for LIMO robot (ROS1): https://bitbucket.org/theconstructcore/agilex_limo/src/master/
- Docker for LIMO robot (ROS2): https://hub.docker.com/repository/docker/theconstructai/limo/general

### **2.1. Install Raspberrypi Desktop**

- Run Raspberry Pi Imager (https://www.raspberrypi.org/software/)
  - select Device: Raspberrypi4
  - select OS: RaspberryPi OS (64Bits) to the SD card
  - Select the configurations:
    - Name: rUBot_XX
    - User: ubuntu
    - Pass: ubuntu1234
    - LAN config: wifi you want to connect (i.e. rUBotics)
    - Regional settings: ES
    - Services: activate ssh
- Insert the SD in a RBPi board and connect an ethernet cable to the router
- power the raspberrypi4 and login:
  - login: ubuntu
  - password: ubuntu1234
- update the OS:
  ````shell
  sudo apt update
  sudo apt upgrade
  sudo reboot
  ````
  - If you want to change the hostname:
  ````shell
  sudo hostnamectl set-hostname nou_hostname
  sudo reboot
  ````
  - If you want to configure a fixed IP:
    - "Edit connections"
    - Select the "Robotics_UB" wifi connection
    - In section "IPv4 settings" Select "Manual"
    - Add IP address and choose the desired IP (192.168.0.61), Netmask (255.255.255.0), Gateway (192.168.0.1)
    - Add DNS server (8.8.8.8) for google DNS
    - Apply and reboot

  ### **2.2. Install VNC connections**

- Connect to the raspberrypi with ssh and activate **VNC connections**:
  - type: sudo raspi-config
  - Navigate to: Interface Options > VNC > Select Yes to enable it.
  - sudo reboot
- In your PC install Remote desktop on RealVNC Viewer: https://www.realvnc.com/es/connect/download/viewer

- If you want to connect to another network, you have to be connected first manually to the different networks to enable raspberrypi to connect to on reboot
- reboot and it will be connected to the first network available

### **2.3. Using VScode remote explorer**

You can install the Extension "Remote explorer" on VScode:

- Open VScode and connect remotelly to the Raspberrypi with ssh -X ubuntu@192.168.xxx.xxx
- If you can not connect to the raspberrypi, perhaps you have to regenerate permissions (replace IP-raspberrypi by 192.168.xx.xx):
  ````shell
  ssh-keygen -R IP-raspberrypi
  ````

### **2.4. Install Docker**

In raspberrypi, add Docker’s official repository for Ubuntu
````shell
sudo apt update
sudo apt upgrade
# install Docker automatically in function of the Raspbian version installed
curl -fsSL https://get.docker.com -o get-docker.sh
sudo sh get-docker.sh
# Start Docker service
sudo systemctl start docker
# Enable Docker to start on boot
sudo systemctl enable docker
sudo systemctl enable containerd.service
# Add your user to the Docker group (to avoid using sudo for Docker commands)
sudo usermod -aG docker $USER
# Reboot to apply changes (especially for the user group change)
sudo reboot
````

**Create a custom Docker image**

We first create a home/ubuntu/Desktop/Docker folder where we place:
- rUBot_mecanum_ws.zip
- Dockerfile
- rubot_bringup.sh (in executable mode!)
- docker-compose.yaml
- .env folder to store the Environment variables (DISPLAY, etc.)

These files are located in this repository on Documentation/files/Docker folder

Follow the instructions:
- Build the Image
````shell
cd /home/ubuntu/Desktop/Docker
docker build -t rubot_ros_noetic_image .
````
- Start the Container
````shell
docker compose up -d
````
- Stop the Container
````shell
docker compose down
````
- Enable Docker to Start on Boot
````shell
sudo systemctl enable docker
````
- To check the running container and to check logs for troubleshooting:
````shell
docker ps
docker logs rubot_ros_noetic_container
````
- To modify the rubot_bringup.sh file: Simply edit rubot_bringup.sh on your host machine. Changes will reflect in the container on the next restart.

To verify if the container is working type on terminal:
````shell
docker exec -it rubot_ros_noetic_container /bin/bash
````

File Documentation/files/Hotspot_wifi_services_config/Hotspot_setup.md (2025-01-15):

# Setup Hotspot

Connect USB-c to GPRS Hotspot controlled by a raspberrypi4
- SD del telefon:
    - Number: 624484300
    - PIN: 1234
- Compte DIGI (https://midigi.digimobil.es/login)
    - User: 624484300
    - Pass: Pepinillo80!
- The Hotspot access point created is:
    - SSID: rUBotics
    - Pass: rUBot123!

To configure the Hotspot you can connect to the raspberrypi with ethernet cable
- es creara una connexio ethernet nova (Eth6)
- Select "Connexions de xarxa", "Wifi", "Properties", "Uso compartido". **UNselect** "Permetre que usuaris d'altres xarxes es connectin a traves de la connexió a internet d'aquest equip". OK.
- Select "Connexions de xarxa", "Wifi", "Properties", "Uso compartido". **Select** "Permetre que usuaris d'altres xarxes es connectin a traves de la connexió a internet d'aquest equip". OK.
- Open Real VNC:
    - Identify the IP raspberry (192.168.137.3)
    - user: pi
    - Password: raspberrypi
- Connect the modem i wait 2on led (net) blinks
- execute in terminal:
````shell
sudo pppd call gprs&
````
- The last line will be:
````shell
Script /etc/ppp/ip-up finished (pid 2050), status = 0x0
````
- execute in terminal:
````shell
sudo route add default ppp0
sudo systemctl restart hostapd
sudo systemctl restart dnsmasq
sudo systemctl restart systemd-networkd
````
- The Bridge rUBotics is ready with IP: 192.168.4.1
- You have to unconnect the ethernet cable

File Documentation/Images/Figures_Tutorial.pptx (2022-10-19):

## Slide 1

Python Publisher Node

Topic

Python Subscriber Node

/listener

/chatter

/talker

std_msgs/String

Message type

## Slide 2

Topic

Node

Topic

/number

/doubler

/doubled

std_msgs/Int32

Message type

std_msgs/Int32

Message type

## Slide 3

Counter exercise

Node 1

Topic 1

Node 2

Topic 2

/number_publisher

/number

/number_counter

/number_count

std_msgs/Int64

Message type

std_msgs/ Int64

Message type

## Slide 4

03_ROS Tutorial Turtlesim

Node

Node

/move_turtle

geometry_msgs.msg/Twist

/turtle1/cmd_vel

/turtlesim

/turtle1/pose

turtlesim.msg/Pose

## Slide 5

Node

/turtle1/color_sensor

turtlesim.msg/Color

/turtle1/cmd_vel

geometry_msgs.msg/Twist

/turtlesim

/turtle1/pose

turtlesim.msg/Pose

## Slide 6

03b_Gopigo3

/motor/encoder/right

Node

/motor/encoder/left

/cmd_vel

geometry_msgs/Twist

/gopigo3

std_msgs/Float64

/odom

nav_msgs/Odometry

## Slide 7

/image_raw

/raspicam_node

sensor_msgs/Image

Node

/scan

sensor_msgs/LaserScan

/ydlidar_node

Node

Node

/rubot_nav

/gopigo3

/cmd_vel

geometry_msgs/Twist

/odom

Node

nav_msgs/Odometry

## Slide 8

/image_raw

/raspicam_node

sensor_msgs/Image

Node

/scan

sensor_msgs/LaserScan

/ydlidar_node

Node

Node

/rubot_nav

/cmd_vel

geometry_msgs/Twist

/rubot

/odom

Node

nav_msgs/Odometry

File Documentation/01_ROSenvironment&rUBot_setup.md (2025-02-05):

# **ROS environment setup**

The rUBot mecanum robot we will work is represented in the picture:

His main characteristics are: 

- RaspberryPi4 computer onboard control with Ubuntu20 and ROS Noetic
  - RPlidar distance sensor
  - usb camera sensor
- Arduino MEGA with shield for sensors & actuators control
  - Servomotor actuators for the 4 mecanum wheels
  


The main objectives of this chapter are:

- Real rUBot setup
- ROS environment setup

You can see graphically the rUBot system setup



We will use TheConstruct environment to:
- Control the rUBot model in virtual environment
- Control the real rUBot in real environment
- Update and syncronize the "rUBot_mecanum_ws" repository project

## **1. Control the rUBot model in virtual environment**

To **setup the repository** in your ROS environment, you need to:
- Fork my repository (https://github.com/manelpuig/rUBot_mecanum_ws) in your github account
- Open your ROS Noetic environment: https://app.theconstructsim.com/
  - Login: robotics.ubx
  - Password: rubot_0x
- Clone your forked directory in your home directory
  ```shell
  cd /home/user
  git clone https://github.com/your_username/rUBot_mecanum_ws
  cd rUBot_mecanum_ws
  catkin_make
  ```
- Open .bashrc and ensure that you have the last 2 lines (review the exact name of your repository):
  ```shell
  source /opt/ros/noetic/setup.bash
  source /home/user/rUBot_mecanum_ws/devel/setup.bash
  ```
You are ready to work with your repository and control the rUBot model in virtual environment!

## **2. Control the real rUBot in real environment**

when you turn on the robot:
- The rUBot connects automatically to a Public "Robotics_UB" Network with a mobile Hotspot.
- Each robot has a Hostname: rUBot_0x
- The static IP assigned to each robot is: 192.168.0.x0
- a "bringup" service is started on boot and the robot is ready to be used 
- each rUBot is registered to the RRL service (Real Robot Lab) from TheConstruct ROS environment (https://www.theconstruct.ai/help/how-do-i-connect-my-own-robot-to-the-construct/)
- Open Your ROSject in "My Rosjects" section
- In the bottom menu select "Connect to your real Robot"
- You will be ready to control the real robot:
  - The bringup is already made in the real robot on boot
  - all the launch files you start on therminal will be executed in the real robot
  - before exit remember to "Disconnect" from your real robot
- before exit the rosject remember to syncronize your repository!

## **3. Update and syncronize the "rUBot_mecanum_ws" repository project**

The objective is to update the changes you have made, when working in ROS environment, in your github repository.

- Access to the TheConstruct environment local repository:
  ````shell
  cd /home/user/rUBot_mecanum_ws
  ````
- Update the local repository with possible changes in github origin repository
  ````shell
  git pull
  ````
- You can work with your local repository for the speciffic project session
- Once you have finished and you want to syncronize the changes you have made and update the github origin repository, type:
  ````shell
  git add .
  git commit -m "Message"
  git push
  ````
- When you will Push them, the first time you will be asked to link the repository to your github account:
- Open a terminal in and type the first time:
  ```shell
  git config --global user.email "mail@alumnes.ub.edu"
  git config --global user.name "your github username"
  ```
- for succesive times, you only need to select changes, Commit a message and Push
- You will have to specify the Username and Password (Personal Access Token you have generated)

To obtain the **PAT** in github follow the instructions:

  - Log in to GitHub
  - Go to Developer Settings
  - Select Access Personal Access Tokens: Choose Tokens (classic)
  - Click Generate new token (classic) and configure it:
    - Add a note to describe the purpose of the token, e.g., "ROS repo sync."
    - Set the expiration (e.g., 30 days, 60 days, or no expiration).
    - Under Scopes, select the permissions required:
      - For repository sync, you usually need: repo (full control of private repositories)
    - Click Generate token
  - Once the token is generated, copy it immediately. You won't be able to see it again after leaving the page.

Your github origin repository has been updated!

## **4. PC connected to the rUBot with virtual Desktop**

In that case the latency is reduced and is optimum fast robot control 

- Connect the PC to the same network as rUBot
- Use nomachine (https://www.nomachine.com/?q=download) remote Desktop to connect the PC to the rUBot with graphical interface

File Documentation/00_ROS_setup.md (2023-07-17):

# **Docker tutorial**

ROS Installation will be made using Docker and we will work and program ROS using Visual Studio Code

## **1. Docker Installation**
Installation instructions could be found in: https://docs.docker.com/desktop/

Some other interessant links could be found:
- http://wiki.ros.org/docker
- http://wiki.ros.org/docker/Tutorials/Docker

You can find a lot of ROS images available. 

Usefull **images that could be opened with browser**:
- ROS_Noetic: https://hub.docker.com/r/arvinskushwaha/ros-noetic-desktop-vnc/tags
- ROS2_Foxy: https://hub.docker.com/r/husarion/ros2-desktop-vnc

The **official images** are mantained by Open Source Robotics Foundation (OSRF).

You can find them in:
- https://registry.hub.docker.com/_/ros/
- https://hub.docker.com/r/osrf/ros/tags

We will use the VNC image to work properly with windows and MAC:
- Open a terminal in your computer and type:
```shell
docker pull arvinskushwaha/ros-noetic-desktop-vnc:latest
```
- Verify the Docker desktop the image installed. 
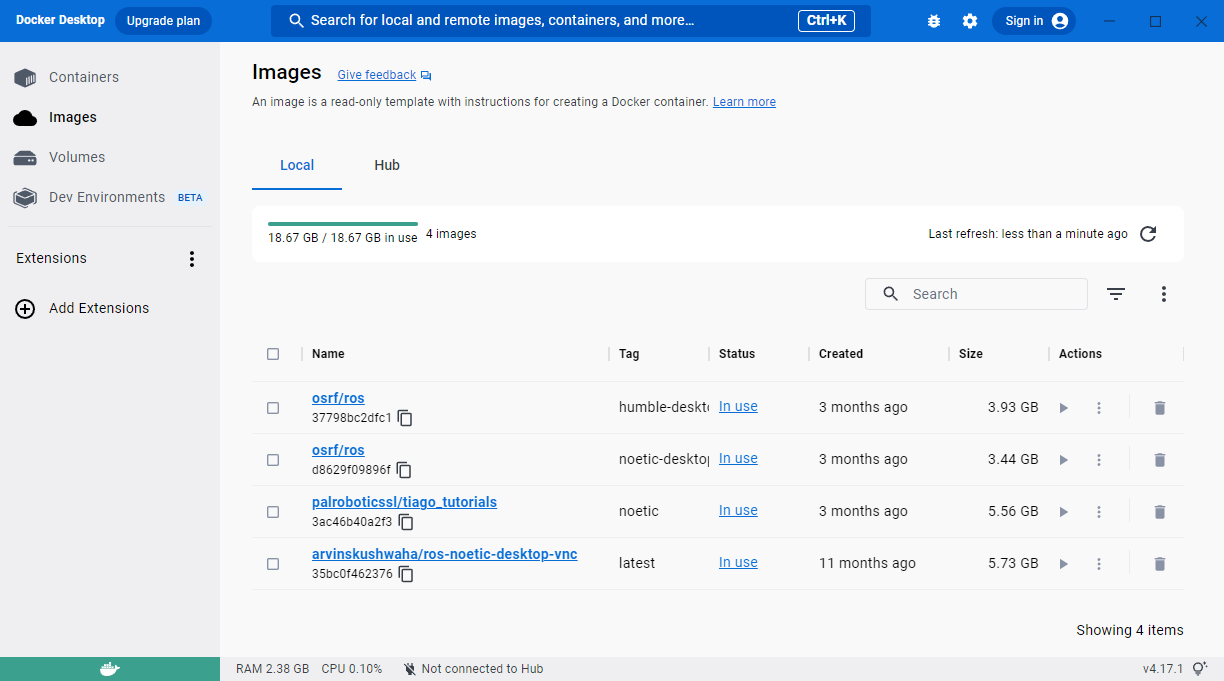
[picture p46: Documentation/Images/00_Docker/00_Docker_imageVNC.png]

- Run The image with the following options:
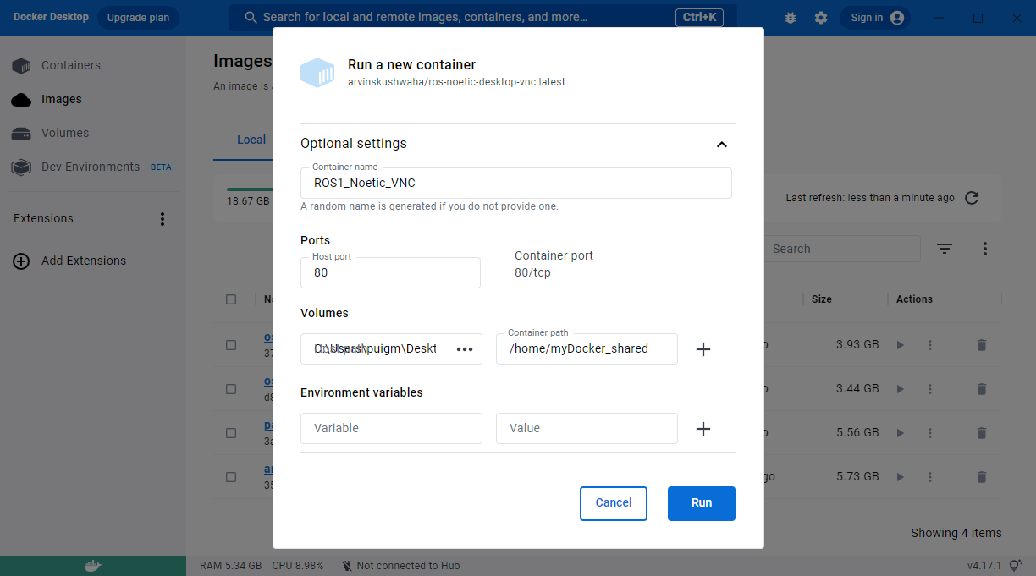
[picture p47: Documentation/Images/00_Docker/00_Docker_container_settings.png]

- Verify the Docker containers created:
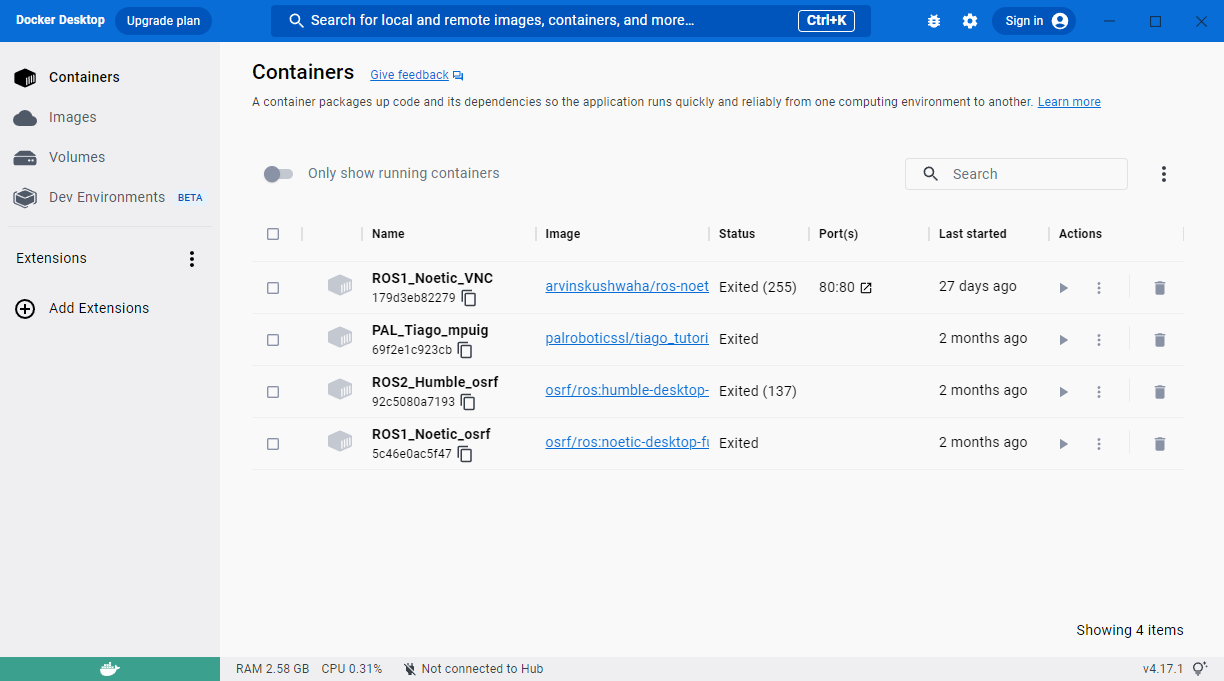
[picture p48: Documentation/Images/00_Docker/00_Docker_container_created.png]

- Run the container in Docker Desktop
- Select in 3-dot menu the option "Open with browser"
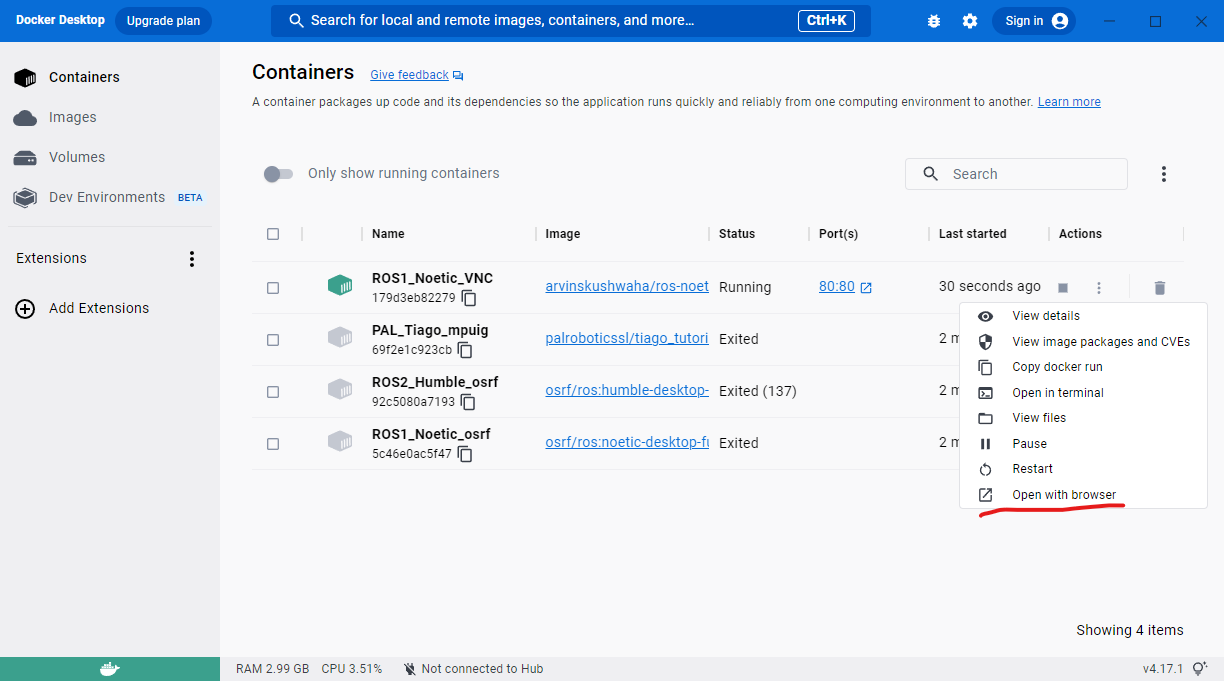
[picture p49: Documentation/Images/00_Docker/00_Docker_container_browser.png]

- A new window appear in your web browser with the graphical interface:
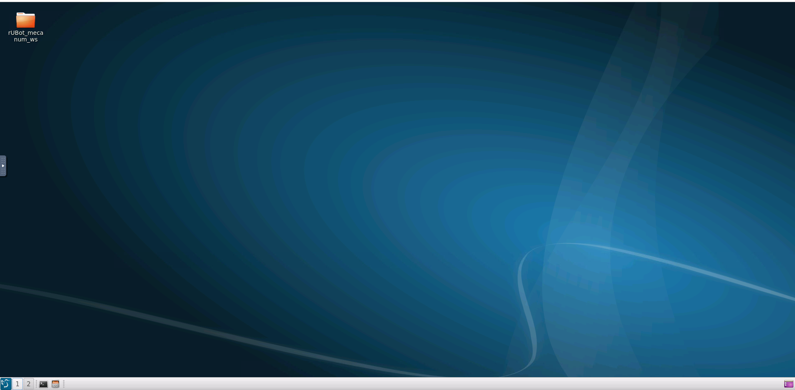
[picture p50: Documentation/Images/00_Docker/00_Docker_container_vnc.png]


You will have now a graphical interface working properly in windows and MAC

## **2. Visual Studio Code with Docker**

The best way to work with ROS within Docker is to use Visual Studio Code

The following extensions have to be installed:
- Docker from Microsoft
- Dev Container from Microsoft

Execute the container and Connect to it within VS Code:
    - from left-side menu choose Docker
    - right-click on the running container and select "Attach VS Code"
- Update your docker Container:
```shell
apt update
apt upgrade
```
>repeat these instructions until you see "All packages are up to date"

- Install some functionalities:
```shell
apt install -y git && apt install -y python3-pip
```
Open the file ".bashrc" on root folder and add the lines at the end
```shell
source /opt/ros/noetic/setup.bash
```
To test Run the Master
```shell
roscore
```

Start another terminal in the same container ID and open turtlesim node.
```shell
source /opt/ros/noetic/setup.bash
rosrun turtlesim turtlesim_node
```

## **3. Clone and syncronize your repository**

You can now **clone** any repository:
- Open a new terminal in /home:
```shell
git clone https://github.com/manelpuig/rUBot_mecanum_ws
cd rUBot_mecanum_ws
source /opt/ros/noetic/setup.bash
catkin_make
```
- Open .bashrc from /root and type at the end:
```shell
source /opt/ros/noetic/setup.bash
source /home/rUBot_mecanum_ws/devel/setup.bash
export GAZEBO_MODEL_PATH=/home/rUBot_mecanum_ws/src/rubot_mecanum_description/models:$GAZEBO_MODEL_PATH
```
- Open a new terminal from any place and verify the correct behaviour

When finished, **syncronize** the changes with your github. 
- Select "Source control" to see the changes you have made
- Select all changes and add a commit message
- When you will Push them, the first time you will be asked to link the repository to your github account:
- Open a terminal in VS Code and type the first time:
```shell
git config --global user.email mail@alumnes.ub.edu
git config --global user.name 'your github username'
```
- for succesive times, you only need to select changes, Commit a message and Push

>You can **update** your repository using web-based Visual Studio Code:
>
>       - pressing "·" key (or add .dev extension)
>       - performing repository modifications
>       - typing "git pull" to syncronize

## **4. Alternative ROS environment**

Mainly for MAC users, if the graphical interface is not working properly, we suggest 2 different solutions:
- Ready to use limited performances web environment
- Use a Virtual machine with virtual box

### **4.1. Ready to use web environment**
You can use the ROS environment developed by "The Construct" (https://app.theconstructsim.com/), enterprise working on ROS academia and development and located in Barcelona.
- Open the link: https://app.theconstructsim.com/
- Create a free user account
- Select "myRosjects"
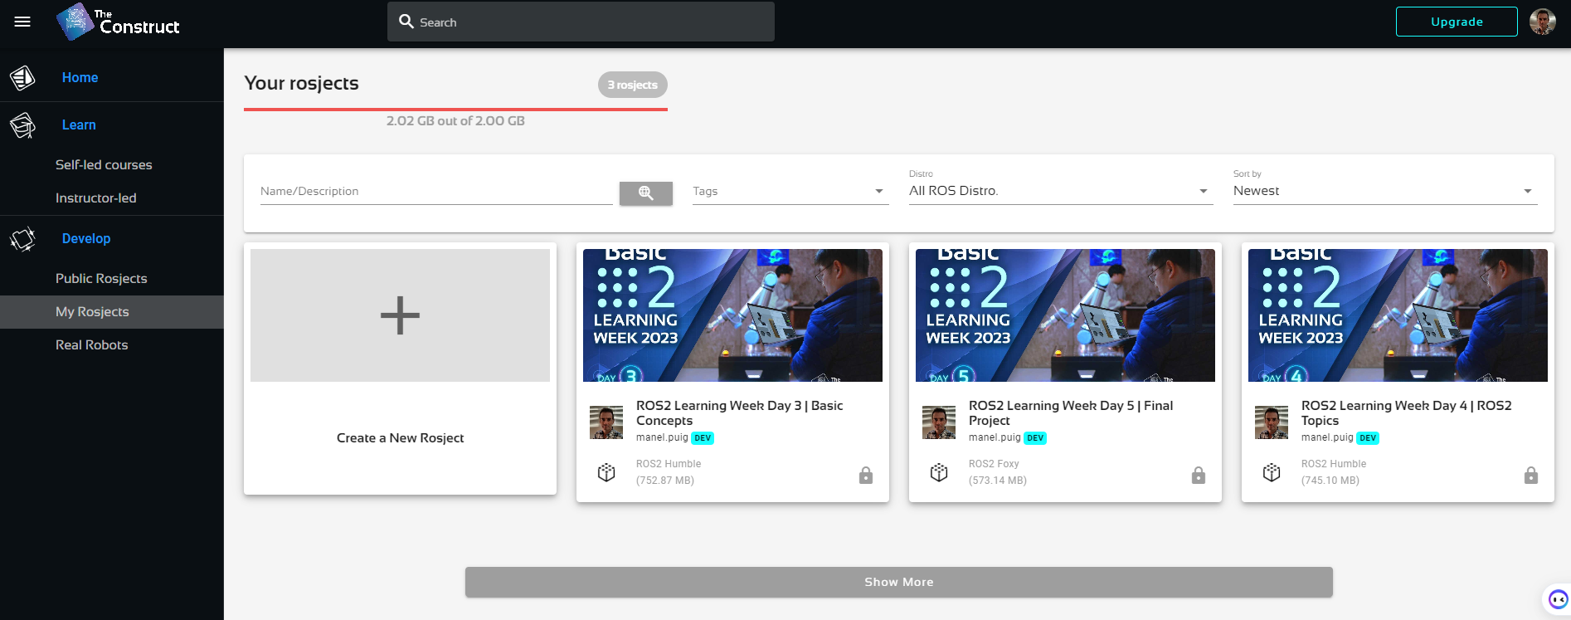
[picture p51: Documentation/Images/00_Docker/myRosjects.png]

- Create a New Project
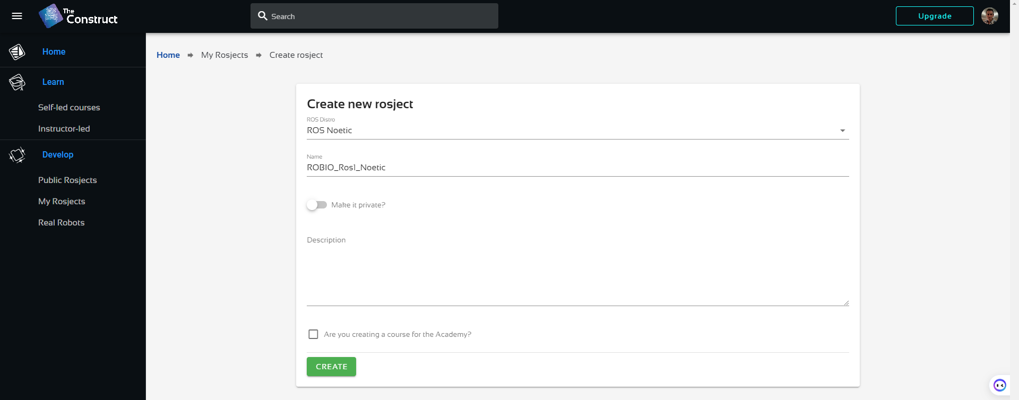
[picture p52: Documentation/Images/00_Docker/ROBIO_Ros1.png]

You will have 2GB Virtual machine with Ubuntu 20 and ROS Noetic installed for free!!

### **4.2. Virtual machine with ROS**
You can always install a ROS virtual machine with Virtual Box for MAC
- Download Virtual Box for macOS systems (https://www.virtualbox.org/wiki/Downloads)
- Install Virtual Box in your computer
- Download the ROS virtual machine in this link:
- and Add this ROS virtual machine choosing file-->Import appliance (and follow instructions)

You will have a ready to use ROS environment

## **5. Software install within Ubuntu Image**

Once you have ubuntu image working properly, mainly for MAC users, you can install SW based on Ubuntu:

### **5.1. roboDK**
Mainly for MAC users, you can install roboDK:
- download the ubuntu version roboDK from: https://robodk.com/download
- Extract executable to /home/roboDK (create first the roboDK folder)
- roboDK icon will appear in Desktop. You can double click to start
- Locate path to python and editor
```shell
which python3
which idle
```
- Place the paths to "Tools --> Options --> Python"

You are ready to use roboDK with python in your Container!

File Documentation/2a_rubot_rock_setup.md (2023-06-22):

# **rUBot mecanum in Rock Install**

The main objectives are:

- Setup the rUBot with rock5b 16GB
- Clone the rUBot workspace to be ready

## **1. Setup the rubot with rock5b**

The rock5b onboard is preinstalled with:
- Ubuntu 20 server 64bits
- NoMachine remote desktop
- ROS Noetic
- Arduino

Insert the SD card in rock5b board and power it. 
- A hotspot will be created:
  - SSID: rock_tplink
  - Pass: rock1234
- Connect your computer to this Hotspot
- Install in your computer Nomachine remote desktop: https://www.nomachine.com/es
- Open Nomachine and connect to the rUBot 
  - Name: the rUBot name
  - Host: 10.42.0.1
  - Port: 4000
  Protocol: NX
- You will be asked for:
  - login: rock
  - password: rock

After few seconds you will have the rUBot desktop in your computer screen!

You will need to perform some configurations:

### **1.1. Hotspot configuration**

In Ubuntu desktop, select "Configuration settings" --> "network" and select "hotspot"

You will have to change the Hotspot name (one for each robot):

Alternativelly you can change the Hotspot settings (name or password) with:
```shell
sudo nm-connection-editor
```
You will be able to change:
- the name: from rock_tplink to rUBot_xx
- The password maintain rock1234

### **1.2. wifi configuration**

The rock5b board have a wireless module (https://es.rs-online.com/web/p/complementos-para-placas-rock/2563901) able to:
- configure a Hotspot
- and a wifi connection

In Ubuntu desktop, select "Configuration settings" --> "network" and select the other wifi connection. 

Select the wifi you want to connect to and type the password. You will now have internet access when you are connected to the rUBot!

## **2. Clone the updated rUBot github repository**

The updated version of rUBot repository is located in:https://github.com/manelpuig/rUBot_mecanum_ws

You will have to:
- In your PC: 
  - Fork this repository to your github account
- In rUBot remote desktop:
  - Open VS Code
  - Clone your github rUBot workspace:
    - Delete the older "rUBot_mecanum_ws" folder
    - open a new terminal in /home/Rock 
    - type:
    ```shell
    cd /home/rock
    git clone https://github.com/your_github_name/rUBot_mecanum_ws
    cd rUBot_mecanum_ws
    catkin_make
    ```
  - Open the .bashrc file in home folder
  - copy these lines at the end
  ```shell
  source /opt/ros/noetic/setup.bash
  source /home/rock/rUBot_mecanum_ws/devel/setup.bash
  export GAZEBO_MODEL_PATH=/home/rock/rUBot_mecanum_ws/src/rubot_mecanum_description/models:$GAZEBO_MODEL_PATH
  ```

  You are ready to work with your robot!

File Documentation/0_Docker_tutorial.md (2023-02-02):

# **Docker tutorial**

ROS Installation will be made using Docker

## **1. Docker Installation & Tools**
We will learn:
- Installation
- Starting docker ROS official images
- Docker getting starter
- Docker with GUI
- Creating custom Docker
- Github sync from docker

### **1.1 Docker Installation**
Installation instructions could be found in:
- http://wiki.ros.org/docker
- http://wiki.ros.org/docker/Tutorials/Docker
- https://docs.docker.com/get-docker/
- https://docs.docker.com/desktop/

In windows:
- download and install: https://docs.docker.com/desktop/install/windows-install/

    >   Open PowerShell terminal and type: systeminfo | find "Tipo de sistema"
    >
    >   The output has to be: x64-based PC
- restart your computer
- Open Docker Desktop
- Then you have to complete your installation with WSL 2 for kernell update in: https://learn.microsoft.com/ca-es/windows/wsl/install-manual#step-4---download-the-linux-kernel-update-package
- Stablish WSL2 as default by opening a powershell and typing: wsl --set-default-version 2
You need also to install Xlaunch for windows for GUI:
- https://sourceforge.net/projects/vcxsrv/

### **1.2 Starting docker ROS official images**
You can find a lot of ROS images available. 

Usefull **images that could be opened with browser**:
- ROS_Noetic: https://hub.docker.com/r/arvinskushwaha/ros-noetic-desktop-vnc/tags
- ROS2_Foxy: https://hub.docker.com/r/husarion/ros2-desktop-vnc

    **Some important trics:**
    - To copy and paste text use the clipboard
    - For home symbol use the "Extra keys"
    - To copy files or folders from/to windows, open a Power Shell terminal and type:
    ```shell
    docker cp c:/Users/puigm/Desktop/road1 Ros1_Noetic:/home/ubuntu/rUBot_mecanum_ws/src/rubot_mecanum_description/models
    docker cp Ros1_Noetic:/home/ubuntu/rUBot_mecanum_ws/src/rubot_mecanum_description/worlds/road1.world c:/Users/puigm/Desktop
    ```
The **official images** are mantained by Open Source Robotics Foundation (OSRF).

You can find them in:
- https://registry.hub.docker.com/_/ros/
- https://hub.docker.com/r/osrf/ros/tags

Interesting information is in:
- https://github.com/noshluk2/ros1_wiki/tree/main/docker

Let's install ROS1 and 2 official image:
```shell
docker pull osrf/ros:noetic-desktop-full
docker pull osrf/ros:foxy-desktop
```
To see all the images installed:
```shell
docker images -a
```
Creating a interactive container from image
```shell
docker run -it osrf/ros:noetic-desktop-full
```
Giving Name to a container while creating
```shell
docker run --name ROS1_Noetic_osrf -it osrf/ros:noetic-desktop-full
```
List of containers:
```shell
docker ps
```
Connect shell to running container
```shell
docker exec -it (container_id) bash
```
Close the container deleting it from Docker Desktop

### **1.3 Docker getting starter**
Lets see a simple Talker-Listener exemple

Run a container with a speciffic name
```shell
docker run --name ROS1_Noetic_osrf -it osrf/ros:noetic-desktop-full
roscore
```
Open a second terminal. Start listener:
```shell
docker exec -it (container_id) bash
source /opt/ros/noetic/setup.bash
rosrun rospy_tutorials listener
```
Open a thirth terminal. Start talker:
```shell
docker exec -it (container_id) bash
source /opt/ros/noetic/setup.bash
rosrun rospy_tutorials talker
```
Stop  container
```shell
docker kill (container_id)
```
### **1.4 Docker with GUI and shared folder**

Running a container with GUI enabled for Windows. We need to create an environment to display the emerging grafic windows.

We need to open XLaunch program and specify the DIPLAY 0. Then run a Docker with this environment:
```shell
docker run --name ROS1_Noetic_osrf -e DISPLAY=host.docker.internal:0.0 --mount src="C:\Users\puigm\Desktop\ROS_github\myPC_shared",dst=/home/myDocker_shared,type=bind -it osrf/ros:noetic-desktop-full
```
- Open Docker Desktop

- Execute the container and Connect to it within VS Code:
    - from left-side menu choose Docker
    - right-click on the running container and select "Attach VS Code"
- Update your docker Container:
```shell
apt update
apt upgrade
```
>repeat these instructions until you see "All packages are up to date"

- Install some functionalities:
```shell
apt install -y git && apt install -y python3-pip
```
To test Run the Master
```shell
roscore
```
Start another terminal in the same container ID and open turtlesim node.
```shell
docker exec -it (container_id) bash
source /opt/ros/noetic/setup.bash
rosrun turtlesim turtlesim_node
```
> Xlaunch has to be opened in lower task menu. Ik errors you have to delete the file CVXServer.0 in C:\Users\HP\AppData\Local\Temp. For that you have to close all applications and restert the computer.

### **1.5. Creating custom Docker**

In Visual Studio code, install the docker extensions:
- Docker (Microsoft)

Then create a new "Dockerfile" with the image configuration:
```python
# This is an example Docker File
#  Command to build it
# docker built -t <image name > .
FROM osrf/ros:noetic-desktop-full

RUN apt-get update
RUN apt-get install -y git && apt-get install -y python3-pip
RUN echo "git and pip Installed"
RUN apt install -y gedit
RUN apt install -y gedit-plugins
RUN echo "gedit Installed"
RUN apt install nautilus -y
RUN apt install gnome-terminal -y
RUN sudo apt install nautilus-actions gnome-terminal -y
RUN echo "Nautilus File manager Installed"

RUN cd /home/

RUN echo "ALL Done"
```
Open a Power Shell terminal in the Dockerfile location and type:
```shell
docker build -t ros1_noetic_mpuig .
```
The Dockerfile is a text file that will produce a Docker Image

Run the image:
```shell
docker run --name ROS1_mpuig -e DISPLAY=host.docker.internal:0.0 -it ros1_noetic_mpuig:latest
```
A "ROS1_mpuig" new container is created. 

For successive times, you have to run direcly the container from Docker Desktop, and open in terminal.

Open Nautilus
```shell
nautilus
```
In a gnome terminal 1 type:
```shell
source /opt/ros/noetic/setup.bash
roscore
```
In a gnome terminal 2 type:
```shell
source /opt/ros/noetic/setup.bash
rosrun turtlesim turtlesim_node
```
The Turtlesim appears in screen

### **1.6. Github sync from docker**

When finished, **syncronize** the changes with your github. 
- Open a terminal in your local repository and type the first time:
```shell
git config --global user.email mail@alumnes.ub.edu
git config --global user.name 'your github username'
git config --global credential.helper store
```
- for succesive times, you only need to do:
```shell
git add -A
git commit -a -m 'message'
git push
```
- you will need to insert the username and the saved PAT password
- syncronize your repository several times to save your work in your github account
> - You can **update** your repository either in your local or **remote repository**:
>   - Local: with the previous instructions
>   - Remote: using web-based Visual Studio Code:
>       - pressing "·" key
>       - performing repository modifications
>       - typing "**git pull**" to syncronize

### **1.7. Clone your repository**

You can now clone any repository:
- Open a new gnome-terminal in /home:
```shell
git clone https://github.com/manelpuig/rUBot_mecanum_ws
cd rUBot_mecanum_ws
source /opt/ros/noetic/setup.bash
catkin_make
```
- Open .bashrc from /root and type at the end:
```shell
source /opt/ros/noetic/setup.bash
source /home/rUBot_mecanum_ws/devel/setup.bash
export GAZEBO_MODEL_PATH=/home/rUBot_mecanum_ws/src/rubot_mecanum_description/models:$GAZEBO_MODEL_PATH
```
- Open a new terminal from any place and verify the correct behaviour

### **1.8. Visual Studio Code with Docker**
You can add Docker extension to your VS Code and connect it to a running Container:
- Add extension "Docker" and "Dev Container"
- Select Docker item in left side
- Select the Docker container you want to connect to
- right-click and select "Attach Visual Studio Code"

A new VS Code windows appears with the runnin container

You can syncronize the changes within github inside VS Code.

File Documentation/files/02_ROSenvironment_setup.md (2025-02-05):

# **ROS environment setup**

The rUBot mecanum robot we will work is represented in the picture:

His main characteristics are: 

- RaspberryPi4 computer onboard control with Ubuntu20 and ROS Noetic
  - RPlidar distance sensor
  - usb camera sensor
- Arduino MEGA with shield for sensors & actuators control
  - Servomotor actuators for the 4 mecanum wheels
  


The main objectives of this chapter are:

- Setup the ROS environment to work with rUBot_mecanum_ws in simulation mode
- Connect the ROS environment with the real rUBot_mecanum

There are different possible solutions for the ROS environment in function of how the real robot is configured:

- If the **rUBot** is connected to a Public Network (recommended)
- If the **rUBot** starts a local hotspot

**Bibliography:**
- https://bitbucket.org/theconstructcore/workspace/projects/PS
- Arduino original program: https://blog.csdn.net/baidu_23831861/article/details/106938752

## **1. rUBot is connected to a Public Network**

When real rUBot is connected to a Public Nerwork we can connect to the real rUBot using:
  - TheConstruct ROS Environment (recommended)
  - WSL ROS environment
  - Docker ROS environment

  

### **1.1. TheConstruct ROS Environment (recommended)**

To **setup the repository** in your ROS environment, you need to:
- Fork my repository in your github account
- Open your ROS Noetic environment: https://app.theconstructsim.com/
- Clone your forked directory in your home directory
  ```shell
  cd /home/user
  git clone https://github.com/yourusername/rUBot_mecanum_ws
  cd rUBot_mecanum_ws
  catkin_make
  ```
- Open .bashrc file with VS Code (open file...)
- Ensure that you have the last 2 lines (review the exact name of your repository):
  ```shell
  source /opt/ros/noetic/setup.bash
  source /home/user/rUBot_mecanum_ws/devel/setup.bash
  ```
You are ready to work with your repository!

To **sync the repository** with the one in your github account, follow the instructions:
- Access to the TheConstruct environment local repository:
  ````shell
  cd /local repository path
  ````
- Update the local repository with possible changes in github origin repository
  ````shell
  git pull
  ````
- You can work with your local repository for the speciffic project session
- Once you have finished and you want to syncronize the changes you have made and update the github origin repository, type:
  ````shell
  git add .
  git commit -m "Message"
  git push
  ````
- You will have to specify the Username and Password (Personal Access Token you have generated)

To obtain the **PAT** in github follow the instructions:

- Log in to GitHub
- Go to Developer Settings
- Select Access Personal Access Tokens: Choose Tokens (classic)
- Click Generate new token (classic) and configure it:
  - Add a note to describe the purpose of the token, e.g., "ROS repo sync."
  - Set the expiration (e.g., 30 days, 60 days, or no expiration).
  - Under Scopes, select the permissions required:
    - For repository sync, you usually need: repo (full control of private repositories)
  - Click Generate token
- Once the token is generated, copy it immediately. You won't be able to see it again after leaving the page.

Your github origin repository has been updated!

To **connect your rUBot mecanum**  to the TheConstruct environment you have to configure your robot to be used in your ROSject. 

The **Instructor** will configure the rUBot:
- In the master **TheConstruct account**, we have to first add a new robot:
  - Open the TheConstruct account and choose "Real Robots". Here you can add your robot.
  - Specify the name and the ROS version
  - Copy the "robot setup code line" used later to setup the robot to the TheConstruct environment

- In the **VScode terminal on rUBot-raspberrypi**:
  - Remember to be connected temporally to the same network as the real rUBot.
  - It is better first to update and upgrade the ubuntu20
  - Paste the "robot setup code line". After some minutes the robot will be properly installed.
  - Run 'source ~/.bashrc' to re-export ROS variables before running roscore.
  - Bringup the robot. This will be done automatically every time the robot is swhitched on.

#### **1.1.1. Robots with Ubuntu20 Desktop**:
- Modify the service to bringup automatically the robot on boot:
  - Stop the servide:
    ````shell
    sudo systemctl stop rubot.service
    ````
  - Make modifications in start_rubot.sh file:
    ````shell
    #!/bin/bash
    source /opt/ros/noetic/setup.bash
    source /home/ubuntu/rUBot_mecanum_ws/devel/setup.bash
    cd /home/ubuntu/rUBot_mecanum_ws
    export ROS_IPV6=on
    export ROS_MASTER_URI=http://master:11311
    export ROS_HOSTNAME=master
    export RMW_IMPLEMENTATION=rmw_cyclonedds_cpp
    export CYCLONEDDS_URI=file:///var/lib/theconstruct.rrl/cyclonedds.xml
    export FASTRTPS_DEFAULT_PROFILES_FILE=/var/lib/theconstruct.rrl/fastdds_husarnet.xml

    roslaunch rubot_mecanum_description rubot_bringup_hw_arduino.launch
    ````
  - Restart the service
    ````shell
    sudo systemctl daemon-reload
    sudo systemctl start rubot.service
    ````
    > If the service was already enabled it is not needed to disable and enable again

#### **1.1.2. Robots with Docker-compose**:
- Install the rUBot_XX on TheConstruct environment (RRL service) to the Raspberrypi OS
- Use the Dockerfile, rubot_bringup.sh and docker-compose.yml files in the Documentation/files/Docker folder
- Note that the environment variables in docker-compose.yml has to be changed:
````shell
name: rubot-noetic
services:
  rubot_ros_noetic_service:
    image: rubot_ros_noetic_image  # No explicit "latest" tag
    privileged: true
    network_mode: host
    container_name: rubot_ros_noetic_container
    environment:
      - ROS_IPV6=on
      - ROS_MASTER_URI=http://master:11311
      - ROS_HOSTNAME=master
      - RMW_IMPLEMENTATION=rmw_cyclonedds_cpp
      - CYCLONEDDS_URI=file:///var/lib/theconstruct.rrl/cyclonedds.xml
      - FASTRTPS_DEFAULT_PROFILES_FILE=/var/lib/theconstruct.rrl/fastdds_husarnet.xml
    volumes:
      - /tmp/.X11-unix:/tmp/.X11-unix:rw
      - /dev:/dev
      - ./rubot_bringup.sh:/root/rubot_bringup.sh:ro
    devices:
      - "/dev/ttyUSB0:/dev/ttyUSB0"
      - "/dev/ttyACM0:/dev/ttyACM0"
      - "/dev/video0:/dev/video0"
    command: ["/root/rubot_bringup.sh"]
    restart: always  # Automatically restart on error or system boot
````
- Stop and remove the Container
````shell
docker compose down
````
- Start and enable the Container
````shell
docker compose up -d
sudo systemctl enable docker
````

The **students** will be able to connect to specific real robot:
- Connect to the proper account: robotics.ub1@gmail.com
- In the **TheConstruct environment ROS_Noetic_course** from "my ROSjects": 
  - Select "Real robots", select the rUBot you have configured previously and "connect"
  - You can control the robot from the same TheConstruct environment you are using for simulation

The real rUBot is usually connected to a public network with "robotics_ub" hotspot and the ROS environment is installed in a PC connected to a public network (the same "robotics_ub" or a different one).

**Uninstall rUBot on TheConstruct**

You have to:
- Uninstall the robot from the TheConstruc web
- Uninstall the rrl service from the rUBot terminal
````shell
rrl-uninstall
````
- Delete the last lines from /etc/hosts related to "husarnet"
- Delete the lines added to .bashrc
- reboot

### **1.2 PC with WSL ROS environment**

Windows Subsystem for Linux is a good method to install a Linux Virtual Machine with ROS in a **windows PC**.

The PC and the robot has to be connected to the same Network

We need to configure Static IP address of WSL (Hyper-V)

### **1.3. PC with Docker ROS environment**

Docker is also a good option to install a ROS Virtual machine. This is compatible for **Windows and MAC**.

The PC and the robot has to be connected to the same Network

- Install and run Docker for windows
- Open VScode and install Docker extension
- Pull an official ROS Image and create a container
````shell
docker pull osrf/ros:noetic-desktop-full
docker run -it --name pc-noetic-container --network host osrf/ros:noetic-desktop-full /bin/bash
````
- Attach the container to VScode
- Configure the .bashrc
````shell
source /opt/ros/noetic/setup.bash
#source /home/ubuntu/rUBot_mecanum_ws/devel/setup.bash
#cd /home/ubuntu/rUBot_mecanum_ws
export ROS_MASTER_URI=http://<rubot-IP>:11311
export ROS_HOSTNAME=<DockerPC-IP>
````
### **1.4. PC connected to the rUBot**

In that case the latency is reduced and is optimum fast robot control 

- Connect the PC to the same network as rUBot
- Use nomachine remote Desktop to connect the PC to the rUBot with graphical interface

## **2. rUBot starts a local hotspot**

When real rUBot starts a local hotspot, we can connect to the real rUBot using:
  - Remote Desktop
  - VScode with grahical interface



### **2.1 Remote Desktop**

To connect your PC to the Robot Hotspot, we have to select the rubot hotspot network:
  - SSID name: rubot_XX 
  - password "rUBot_Mec"

We will use Nomachine as a remote Desktop, select:
- IP address: 10.42.0.1
- user: ubuntu
- password: ubuntu1234

For a proper Display resolution in Nomachine, select: Display --> Change the size of remote screen

You will have the rUBot desktop on your windows nomachine screen

You are ready to work for the laboratory session!

### **2.2. VS code with graphical display**

To connect your computer to the robot using VS code with "Remote Explorer" extension installed:
- Open VS code and select "Remote Explorer"
- Add a new SSH connection as: "ssh -X ubuntu@10.42.0.1"
- Verify on ssh/settings "ForwardX11 yes" and "user ubuntu" 
- After connection specify the password as "ubuntu1234"

>Note: When you connect to your rUBot from another computer, you will have perhaps to regenerate the KEYS. In a new cmd on your PC, type the instuction and you will be able to connect with VScode:
````shell
ssh-keygen -R 10.42.0.1
````

You are now inside the rUBot_xx raspberrypi!

To finish, follow the steps:
- in a VScode rUBot terminal type:
````shell
sudo poweroff
````
- in VS code choose "Close remote connection"

You will be automatically disconnected from VS code and after 1 minute, you can switch off the raspberryPi.

**Graphical display**
To have graphical display we need:
- In your PC: Install Xlaunch
  - Download and install "Xming X Server for Windows" from: https://sourceforge.net/projects/xming/
  - Start XLaunch and in first window choose "Multiple windows" and Display "0"
  - in second window select "Start no client".
  - In the third window, ensure that "Disable access control" is selected (this allows your Raspberry Pi to connect).
  - Finish the setup and let XLaunch run in the background.
- Obtain the IP of your PC using "cmd" and type "ipconfig" (i.e. 10.42.0.78)
- In VScode raspberrypi4:
  - update and upgrade the raspberrypi ubuntu
  - Perhaps the firewall will block the connection, you have to create a new firewall rule:
    - Open the Windows Defender Firewall settings.
    - Go to Advanced Settings.
    - Create a new inbound rule:
      - Rule Type: Custom
      - Program: All programs
      - Protocol: TCP
      - Local Port: All ports
      - Remote IP Address: 10.42.0.0/24
      - Action: Allow the connection
      - Profile: Check only "Private" to allow traffic when connected to private networks.
  - reboot
  - Add to .bashrc file the lines: 
  ````shell
  export DISPLAY=10.42.0.78:0.0
  source /opt/ros/noetic/setup.bash
  source /home/ubuntu/Desktop/rUBot_mecanum_ws/devel/setup.bash
  ````

Graphical windows will be displayed in your PC Display!

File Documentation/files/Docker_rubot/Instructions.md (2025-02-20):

# Instructions for LIMO in ROS1

Estos son los pasos para implementar el fix:
Para el docker si está corriendo: docker compose -f /path/to/agilex_limo/limo_ros/docker/docker-compose.yaml down (si mal no recuerdo, el path en donde estaba era ~/agilex_limo/limo_ros/docker/docker-compose.yaml)
Prune de docker para borrar caché: docker system prune
git pull de nuestro repositorio agilex_limo: cd ~/agilex_limo/ && git pull
Corre el docker en background: docker compose -f ~/agilex_limo/limo_ros/docker/docker-compose.yaml up -d
Para arreglar el mismo problema pero en tu RUbot, aquí tienes las adiciones que he hecho en agilex_limo, que podrás traspasar a cualquier robot en noetic:

https://bitbucket.org/theconstructcore/agilex_limo/commits/6d180fac825410b5212ebfd329b3bc622fb8fcdd

Creo que el problema es que en tu robot LIMO, no has dado los permisos suficientes a docker. Es por esto que tienes que agregar sudo a cada comando de docker. Es muy importante en este fix que haya permisos de docker. Puedes hacerlo de esta forma: (https://docs.docker.com/engine/install/linux-postinstall/#manage-docker-as-a-non-root-user) 
Create docker group: sudo groupadd docker
Add user to group: sudo usermod -aG docker $USER
Log out and log back in for groups to be evaluated.
Test docker ps without sudo. It should work.

Lo que hacer es lo siguiente (ya con los permisos de docker suficientes):
Si ya tienes un LIMO registrado, no lo borres. Simplemente copia el comando que compartí en el screenshot y pégalo dentro del LIMO.
Asegúrate de que no haya ningún docker container corriendo.
docker system prune en el LIMO
Corre el docker-compose.yaml actualizado: https://bitbucket.org/theconstructcore/agilex_limo/src/master/limo_ros/docker/docker-compose.yaml
Sin hacer nada más dentro del robot, connecta al LIMO dentro de nuestra plataforma.
Haz test de movimiento de ruedas.
Desconecta/conecta desde nuestra web.
Haz test de movimiento de ruedas.

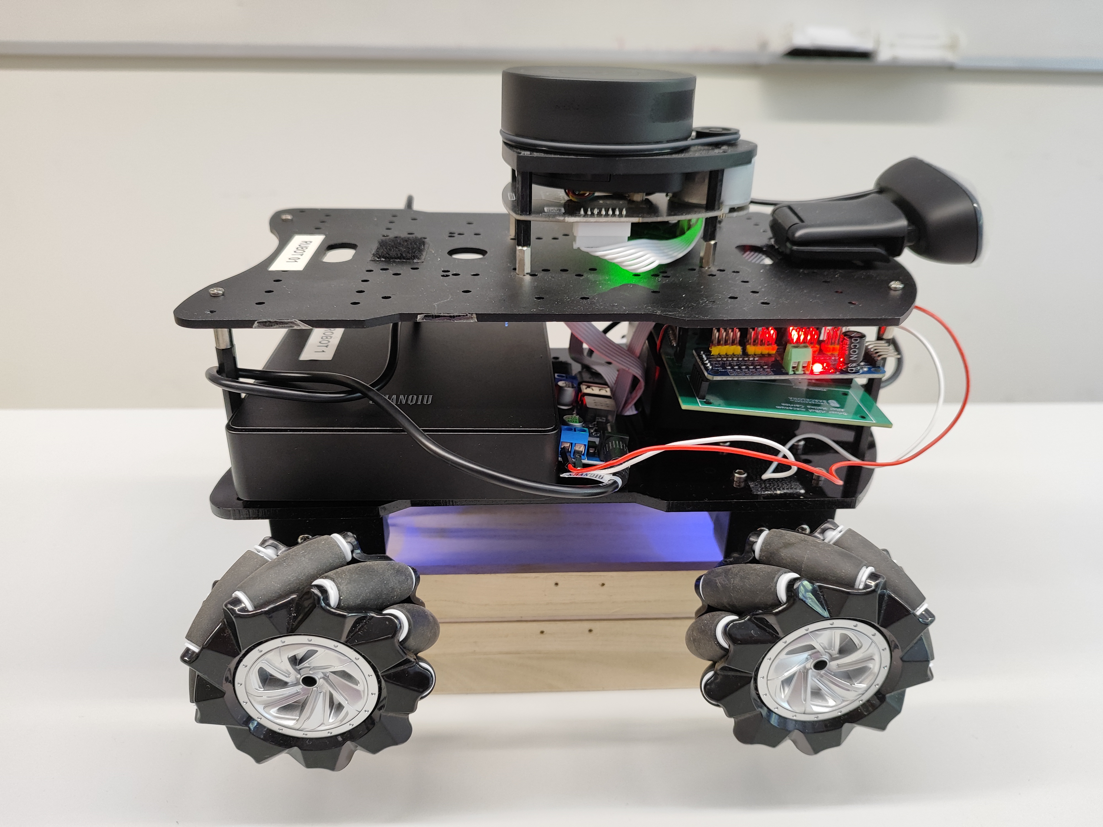
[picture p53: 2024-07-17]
Documentation/Images/01_Setup/01_rubot_pi1.jpg

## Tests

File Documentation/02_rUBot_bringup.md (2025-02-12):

# **rUBot mecanum Bringup**

The objectives of this chapter are:
- Create a robot model of our rUBot mecanum
- Create a world model of the virtual environment
- Bringup the robot in virtual environment
- Bringup the real robot.

The rUBot mecanum robot we will work is represented in the picture:


**Bibliography:**
- https://bitbucket.org/theconstructcore/workspace/projects/PS

## **1. rUBot mecanum model generation**

First of all, we have created the "rubot_mecanum_description" package where we have created the rUBot model. 

In case you want to create it from scratch, type:
```shell
cd /home/user/rubot_mecanum_ws/src
catkin_create_pkg rubot_mecanum_description rospy
cd ..
catkin_make
```

### **1.1. Model design**

The geometrical definition of our rUBot is graphically described by:


The different elements (named **links**) are:
- base_link
- wheels
- camera
- base_scan

These elements are connected each-other by **joints**:
- base_link_joint
- wheel_joint
- joint_camera
- scan_joint

Some of these links have a speciffic **functionalities**:
- wheels: perform a robot movement according to a Mecanum-drive kinematics
- camera: view front images
- base_scan: detect obstacle distances in 360º around the robot

To create our robot model, we use **URDF files** (Unified Robot Description Format). URDF file is an XML format file for representing a robot model.(http://wiki.ros.org/urdf/Tutorials)

The general structure of a robot urdf model is based on:
- Links and joints: for the geometrical structure
- Gazebo plugins: for the functionalities

The urdf file structure is:
```xml
<?xml version="1.0" encoding="utf-8"?>
<robot name="rubot">
  <link name="base_link">
  ...
  </link>
  <joint name="base_link_joint" type="fixed">
  ...
  </joint>
  <gazebo>
    <plugin name="Mecanum_controller" filename="libgazebo_ros_planar_move.so">
    ...
    </plugin>
  </gazebo>
  <gazebo reference="upper_left_wheel">
  ...
  </gazebo>
</robot>
```

We have created 2 folders for model description:
- URDF: folder where different URDF models are located. In our case rubot.urdf
- meshes: folder where 3D body models in stl format are located. We will have rubot folder.

As we have explained above, main parts of URDF model are:
- links: diferent bodies/plastic elements
- joints: connection between 2 links 
- sensors & actuators plugins (2D camera, LIDAR and 4-wheels mecanum-drive)

The **link definition** contains:
- visual properties: the origin, geometry and material
- collision properties: the origin and geomnetry
- inertial properties: the origin, mass and inertia matrix

The **joint definition** contains:
- joint Type (fixed, continuous)
- parent and child frames
- origin frame
- rotation axis

In the case or upper left wheel link:
```xml
<!-- upper_left_wheel -->
  <link name="upper_left_wheel">
    <visual>
      <origin rpy="0 0 0" xyz="0 0 0"/>
      <geometry>
        <mesh filename="package://rubot_mecanum_description/meshes/rubot/upper_left_wheel.stl" scale="0.001 0.001 0.001"/>
      </geometry>
      <material name="light_grey"/>
    </visual>
    <collision>
      <origin rpy="-1.57 0 0" xyz="0 0 0"/>
      <geometry>
        <cylinder length="0.03" radius="0.05"/>
      </geometry>
    </collision>
    <inertial>
      <origin rpy="-1.57 0 0" xyz="0.0 0.0 0.0"/>
      <mass value="0.2"/>
      <inertia ixx="0.000166" ixy="0" ixz="0" iyy="0.000303" iyz="0" izz="0.000166"/>
    </inertial>
  </link>
  <joint name="upper_left_wheel_joint" type="continuous">
    <origin rpy="0 0 0" xyz="0.07 0.1 0"/>
    <parent link="base_link"/>
    <child link="upper_left_wheel"/>
    <axis xyz="0 1 0"/>
  </joint>
```
> Be careful with base_link:
>
> The inertia matrix can be analytically calculated with the mass and geometry. Be sure the mass is consistent and the inertia Ixx,Iyy and Izz are high enough to avoid underired drift movements. Consider the Inertia matrix you can generate using the **urdf_inertial_calculator.py** program file you have in "Documentation/files/Doc/Robot_Models/URDF_inertial".

The rUBot model includes different **sensors and actuators**:

The full model contains also information about the sensor and actuator controllers using specific **Gazebo plugins** (http://gazebosim.org/tutorials?tut=ros_gzplugins#Tutorial:UsingGazebopluginswithROS). 

Gazebo plugins give your URDF models greater functionality and compatiblility with ROS messages and service calls for sensor output and motor input. 

These plugins can be referenced through a URDF file, and to insert them in the URDF file, you have to follow the sintax:

**2D-camera Sensor**:

The two-dimensional camera sensor corresponds to the USB real camera. 

This camera obtains 2D images in the front and is simulated in URDF model as:
- link with the visual, collision and inertial properties
- joint of fixed type
- Gazebo plugin as a sort of "driver" to simulate the real behaviour

Review the joint and link definition in URDF model.

The used Gazebo plugin is:

```xml
  <!-- 2D Camera controller -->
  <gazebo reference="camera">
    <sensor name="camera1" type="camera">
      <update_rate>30.0</update_rate>
      <camera name="front">
        <horizontal_fov>1.3962634</horizontal_fov>
        <image>
          <width>800</width>
          <height>800</height>
          <format>R8G8B8</format>
        </image>
        <clip>
          <near>0.02</near>
          <far>300</far>
        </clip>
      </camera>
      <plugin filename="libgazebo_ros_camera.so" name="camera_controller">
        <alwaysOn>true</alwaysOn>
        <visualize>true</visualize>
        <cameraName>rubot/camera1</cameraName>
        <imageTopicName>image_raw</imageTopicName>
        <cameraInfoTopicName>camera_info</cameraInfoTopicName>
        <frameName>camera</frameName>
        <hackBaseline>0.07</hackBaseline>
        <distortionK1>0.0</distortionK1>
        <distortionK2>0.0</distortionK2>
        <distortionK3>0.0</distortionK3>
        <distortionT1>0.0</distortionT1>
        <distortionT2>0.0</distortionT2>
      </plugin>
    </sensor>
  </gazebo>
  ```
>To view the camera image you can:
> - add the line in the plugin 
> ```xml
><visualize>true</visualize>"
> ```
> - use rviz
> - type rqt in a terminal and select Plugins->Visualization->Image View
>
>Alternativelly with false in plugin, you can allways call the image typing in a new terminal:
>```shell
>rqt image view
>```

**RPlidar sensor**

A Lidar sensors is  device that is able to measure the obstacle distances at 360º around the robot. 

He is sending 720 laser beams (2 beams/degree) and measures the distance each laser beam finds an obstacle. He is able to measure from 12cm to 10m. The used Lidar sensor is a 360º RPLidar A1M8 (https://www.robotshop.com/es/es/rplidar-a1m8-kit-desarrollo-escaner-laser-360-grados.html)

This lidar is simulated in URDF model as:
- link with the visual, collision and inertial properties
- joint of fixed type
- Gazebo plugin as a sort of "driver" to simulate the real behaviour

 Review the joint and link definition in URDF model.
> Note that rpLIDAR is mounted at 180º and you need to turn the link model and the joint to reflect this in the URDF model.



The gazebo plugin we have used is:
```xml
  <!-- Laser Distance Sensor RPLIDAR controller-->
  <gazebo reference="base_scan">
    <sensor name="lds_lfcd_sensor" type="ray">
      <pose>0 0 0 0 0 0</pose>
      <visualize>true</visualize>
      <update_rate>5</update_rate>
      <ray>
        <scan>
          <horizontal>
            <samples>720</samples>
            <resolution>1</resolution>
            <min_angle>0.0</min_angle>
            <max_angle>6.28319</max_angle>
          </horizontal>
        </scan>
        <range>
          <min>0.12</min>
          <max>10</max>
          <resolution>0.015</resolution>
        </range>
        <noise>
          <type>gaussian</type>
          <!-- Noise parameters based on published spec for YDLIDAR X4
              is 1.5% at half range 4m (= 60mm, "+-160mm" accuracy at max. range 8m).
              A mean of 0.0m and stddev of 0.020m will put 99.7% of samples
              within 0.16m of the true reading. -->
          <mean>0.0</mean>
          <stddev>0.02</stddev>
        </noise>
      </ray>
      <plugin filename="libgazebo_ros_laser.so" name="gazebo_ros_lds_lfcd_controller">
        <!-- topicName>/gopigo/scan</topicName -->
        <topicName>scan</topicName>
        <frameName>base_scan</frameName>
      </plugin>
    </sensor>
  </gazebo>
```
>To view the LIDAR rays be sure to add 
> ```xml
><visualize>true</visualize>"
> ```
> or use rviz

It is important to note that:
- the number of points of real RPLidar depends on Lidar model (you will need tot test it first)
- the number of points of simulated Lidar is selected to 720

**Actuator**:

The rUBot_mecanum contains a "Mecanum drive actuator" based on:
- 4 wheels driven by a DC servomotor 
- with speciffic Kinematic control 
- able to move the robot in x and y directions
- and able to obtain the Odometry information

Gazebo plugin is a sort of "driver" to simulate the Kinematics of our rUBot_mecanum.

The **rUBot_mecanum kinematics** describes the relationship between the robot wheel speeds and the robot velocity. We have to distinguish:
- **Forward kinematics**: obtains the robot velocity (linear and angular in /cmd_vel) and POSE (odometry) for speciffic robot wheel speeds
- **Inverse kinematics**: obtains the robot wheels speeds for a desired robot velocity (linear and angular in /cmd_vel)

The different movements the Mecanum robot is able to perform are:



This kinematics and odometry calculations are described in the "libgazebo_ros_planar_move.so" file and the URDF model will contain the specific gazebo plugin.

This driver is the "Planar Move Plugin" and is described in Gazebo tutorials: http://gazebosim.org/tutorials?tut=ros_gzplugins#AddingaModelPlugin

```xml
  <!-- Mecanum drive controller -->
  <gazebo>
    <plugin name="Mecanum_controller" filename="libgazebo_ros_planar_move.so">
      <commandTopic>cmd_vel</commandTopic>
      <odometryTopic>odom</odometryTopic>
      <odometryFrame>odom</odometryFrame>
      <odometryRate>50.0</odometryRate>
      <robotBaseFrame>base_footprint</robotBaseFrame>
    </plugin>
  </gazebo>
  ```

### **1.2. ROS visualization Tools**

ROS has two powerfull visualization tools:
- RVIZ: used to visualize the robot model and the messages published in the different topics
- Gazebo: is a physical simulator 

**RVIZ**

We will first use RVIZ to check that the model is properly built. 

RViz only represents the robot visual features. You have available all the options to check every aspect of the appearance of the model.

We use a specific "display.launch" launch file where we specify the robot model we want to open in rviz with a configuration specified in "urdf.rviz":
```xml
<launch>
  <param name="robot_description" textfile="$(find rubot_mecanum_description)/urdf/rubot.urdf" />
  <node name="joint_state_publisher" pkg="joint_state_publisher" type="joint_state_publisher" />

  <node name="robot_state_publisher" pkg="robot_state_publisher" type="robot_state_publisher" />
  <node name="rviz" pkg="rviz" type="rviz" args="-d $(find rubot_mecanum_description)/rviz/urdf_final.rviz" />
</launch>
```
```shell
roslaunch rubot_mecanum_description rubot_rviz.launch
```


> Colors in rviz: 
>- are defined at the beginning
>- Ensure the "visual" link properties have color "name"
```xml
<robot name="rubot">
  <material name="yellow">
    <color rgba="0.8 0.8 0.0 1.0"/>
  </material>

  ...

    <link name="base_link">
    <visual>
      <origin rpy="0 0 0" xyz="0 0 0"/>
      <geometry>
        <mesh filename="package://rubot_mecanum_description/meshes/rubot/base_link.stl" scale="0.001 0.001 0.001"/>
      </geometry>
      <material name="yellow"/>
    </visual>
```
**Gazebo**

In robotics research, always before working with a real robot, we simulate the robot behaviour in a virtual environment close to the real one. **Gazebo** is an open source 3D robotics simulator and includes an ODE physics engine and OpenGL rendering, and supports code integration for closed-loop control in robot drives. This is sensor simulation and actuator control.

We will create a new rubot_gazebo.launch file to spawn the robot in an empty world:
```xml
<launch>
  <!-- Define the needed parameters -->
  <arg name="model" default="rubot.urdf" />

  <include file="$(find gazebo_ros)/launch/empty_world.launch"/>
  <!-- Spawn the robot -->
  <!-- Robot URDF definition -->
    <param name="robot_description" textfile="$(find rubot_mecanum_description)/urdf/$(arg model)"/>
  <node name="spawn_model" pkg="gazebo_ros" type="spawn_model"
    args="-urdf -model rUBot -param robot_description"/>
</launch>
```
Open a new terminal and launch this file:
```shell
roslaunch rubot_mecanum_description rubot_gazebo.launch
roslaunch rubot_mecanum_description rubot_rviz.launch
```


You will see in Rviz the camera is receiving now images!
> Colors in gazebo: 
>- are defined at the end of urdf file:
```xml
<!-- Gazebo colors have to be specified here with predefined Gazebo colors -->
  <gazebo reference="base_link">
    <material>Gazebo/Yellow</material>
  </gazebo>
```
You can create a very **simple world** "rubot.world" using gazebo:

- Maintain the Gazebo and RVIZ screens opened
- add some objects in the empty world

Now in RVIZ you will see the objects with the USB camera and Lidar

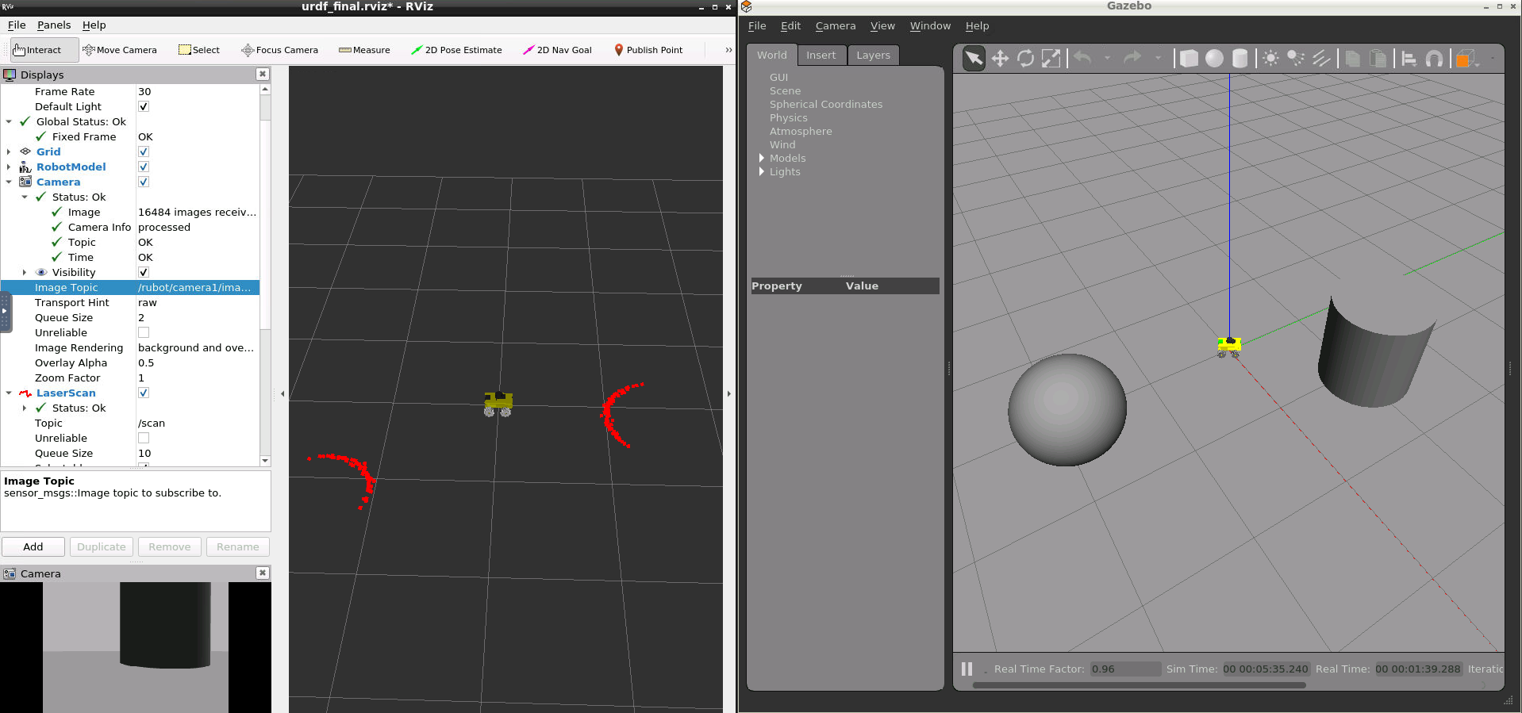
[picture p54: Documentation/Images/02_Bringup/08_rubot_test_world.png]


You can see the nodes and topics generated using rqt_graph
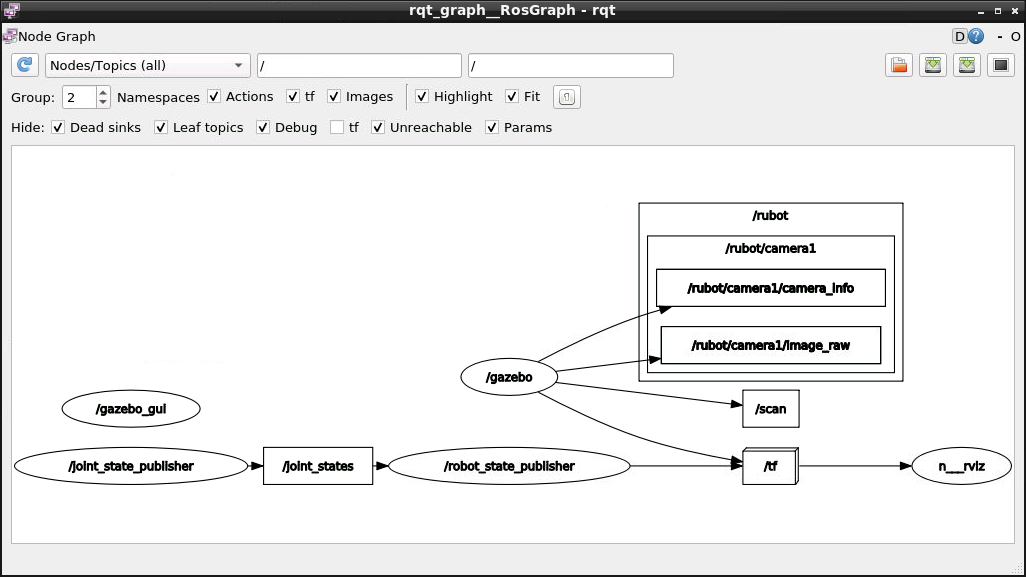
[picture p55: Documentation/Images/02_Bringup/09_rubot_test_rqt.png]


> To see the frames you have to add TF in rviz

>Carefull:
- Perhaps is needed to setup your Keys again:
  ```shell
  curl -s https://raw.githubusercontent.com/ros/rosdistro/master/ros.asc | sudo apt-key add -
  sudo apt get update
  sudo apt get upgrade
  ```
- To close the Gazebo is better to type in a new terminal:
  ```shell
  pkill gzserver && pkill gzclient
  ```

## **2. Design the project world**

Here we have first to design the project world, for exemple a maze from where our rUBot mecanum has to navigate autonomously.

There is a very useful and simple tool to design a proper world: "**Building editor**" in gazebo.

Open gazebo as superuser:
```shell
sudo gazebo
```

You can build your world using "Building Editor" in Edit menu



- Save the generated model in a model folder (without extension)
- Close the Builder Editor, modify the model position and add other models to configure your virtual desired world.
- Save the generated world (with extension .world) in the world folder.

Once you finish is better to close the terminal you have work as superuser

#### ***Modify a created world***
- Open a terminal where you have the world you want to modify
- type: sudo gazebo ./test.world (or simply "gazebo test.world")
- make modifications: add some other models, delete previously added models, etc.
- save your world in a world directory
- close gazebo and the terminal
#### **Create world with model parts**
You can create model parts like walls of 60cm or 90cm or 120cm with a geometry and color, using building editor. These parts can be saved:
- in ~/.gazebo/models/ (this is the default folder)
- in speciffic folder in your package (i.e. rUBot_mecanum_ws/src/rubot_mecanum_description/models). In this case, to add the path in Gazebo, add this line in .bashrc file:
  ```xml
  export GAZEBO_MODEL_PATH=/home/user/rUBot_mecanum_ws/src/rubot_mecanum_description/models:$GAZEBO_MODEL_PATH
  ```
- When a model is created with "Building Editor", this path is saved in gazebo environment and you can use it in the future.
- You can allways select "Add folder path" in "insert" gazebo menu tab, and select the models folder you have created in your project ws 

You will have acces in gazebo insert section. Then you can construct your world adding parts.

This is an exemple:
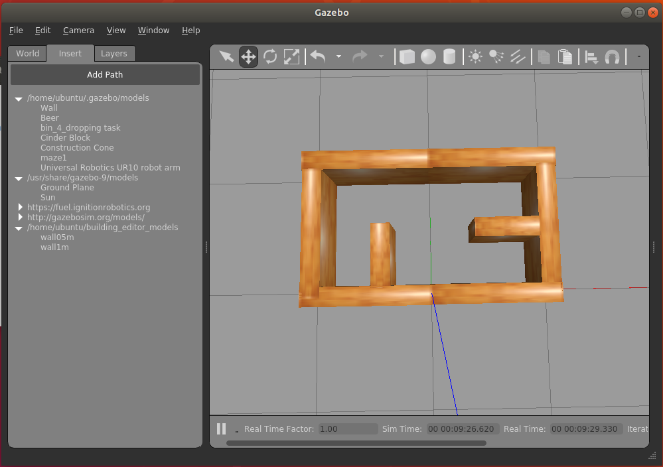
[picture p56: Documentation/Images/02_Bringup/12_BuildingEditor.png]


## **3. Bringup the rUBot in Virtual environment**

The first step in robotics is to bringup the rUBot mecanum robot in our generated virtual world. This means:
- Open Gazebo with the designed virtual world
- spawn our robot in the designed virtual world 
- and open Rviz to see the topic messages.

This is defined in "rubot_bringup_sw.launch" file. 
``` shell
roslaunch rubot_mecanum_description rubot_bringup_sw.launch
```
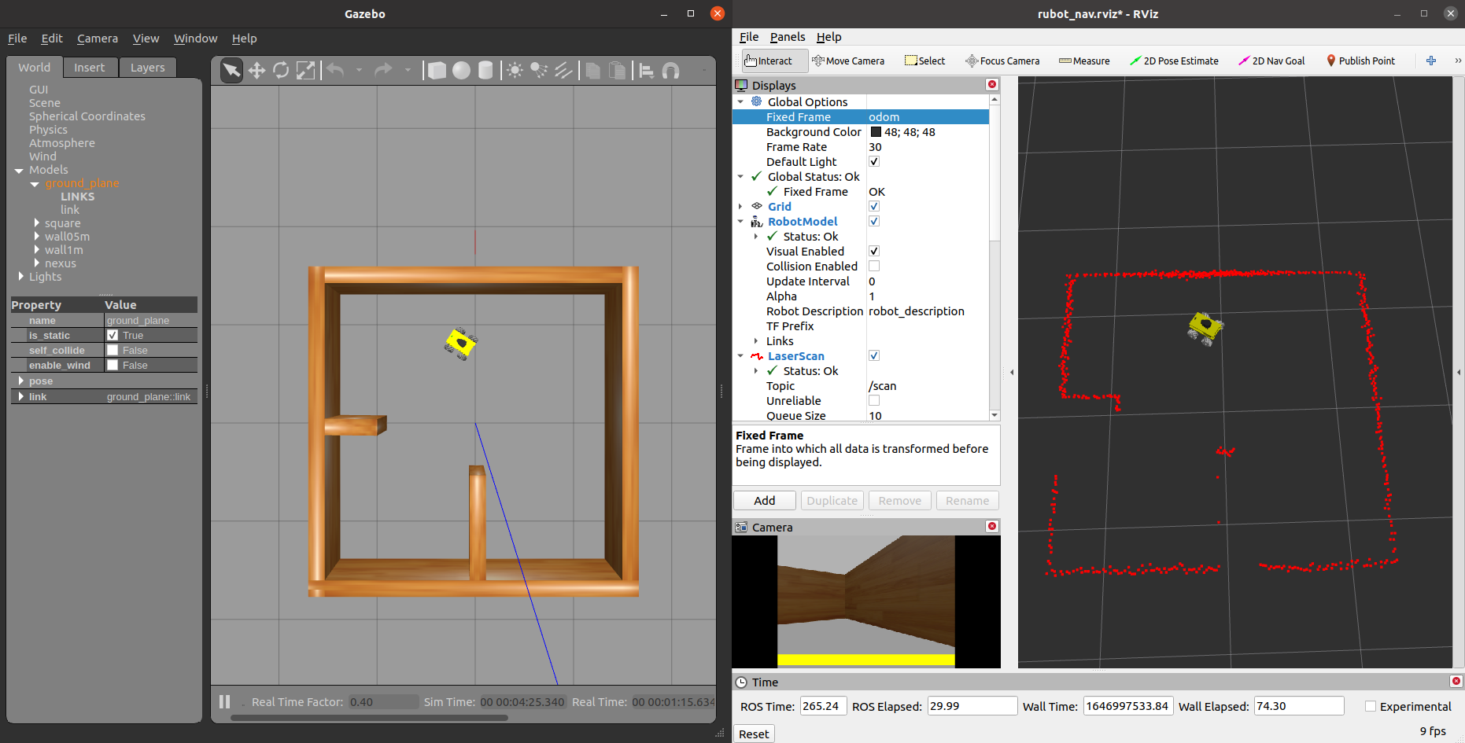
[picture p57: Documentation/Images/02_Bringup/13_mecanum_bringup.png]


>Careful:
- we have included in launch file: gazebo rubot spawn and rviz visualization 
- Verify in rviz you have in fixed frame the "odom" frame

Now we are ready to control our robot in this virtual environment!

**Activity: rUBot Bringup SW**

The objective of this activity is to spawn our custom rUBot in a virtual world.

You will have to:
- Design a custom rUBot model corresponding to the real rUBot_mecanum (rubot_custom.urdf), with:
  - Customized model colors (rviz and gazebo)
  - Add a 3D-part on top with a fixed joint
- Design a custom virtual world using the wooden model parts

To verify the final bringup, create a new "rubot_bringup_sw.launch" file with your rubot_custom.urdf and the world you have created:
```shell
roslaunch rubot_mecanum_description rubot_bringup_sw.launch
```
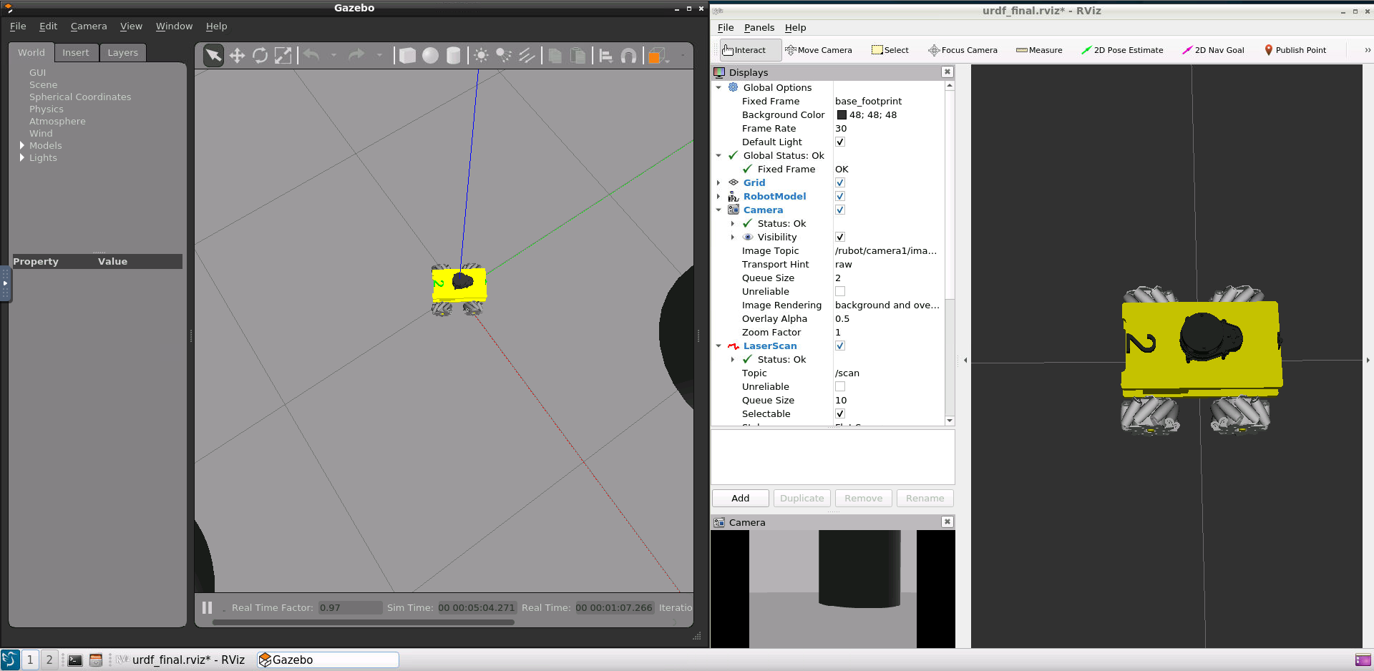
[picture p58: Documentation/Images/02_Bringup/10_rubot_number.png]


Upload a zip file with:
- Picture with gazebo and rviz obtained with your custom rubot model and designed world
- file: "rubot_custom.urdf"
- file: "rubot_bringup_sw_custom.launch"

## **4. Bringup the real robot**

The rUBot Mecanum real hardware is based on:
- Robot base structure with 4 Mecanum wheels driven by DC-servomotors
- 2D-Camera to generate front images
- Lidar for Navigation with obstacle avoidance
- Arduino Mega with custom Shield: to control the 4 Mecanum Wheels (and other sensors onboard in function of the application)
- Raspberrypi4b Computer on-board: for high level control in ROS environment. He will also control directly the usb-camera and the Lidar.

To Bingup our real robot we have to:
 
- Launch the "Mecanum-drive control" module for servomotor actuators for the 4 mecanum wheels
- Launch the RPlidar distance sensor
- Launch the usb camera sensor



### **4.1. Launch the "Mecanum-drive control" module**

The 4 mecanum wheels will be controlled by a Arduino Mega shield based control board.

Let's see some important characteristics:
- You need to install Encoder.h lib: https://www.arduino.cc/reference/en/libraries/encoder/
- Verify the Motor connections order

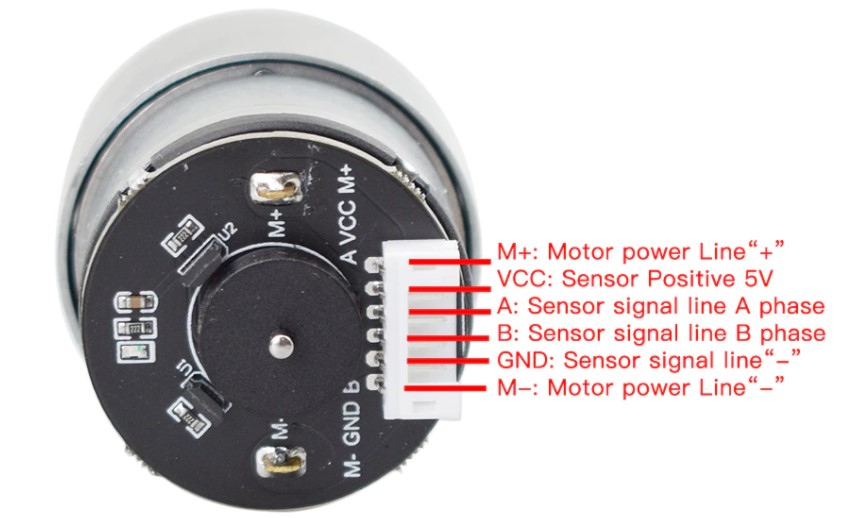
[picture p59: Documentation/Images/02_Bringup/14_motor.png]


- Verify the Shield schematics for the A,B,C,D bus-connectors

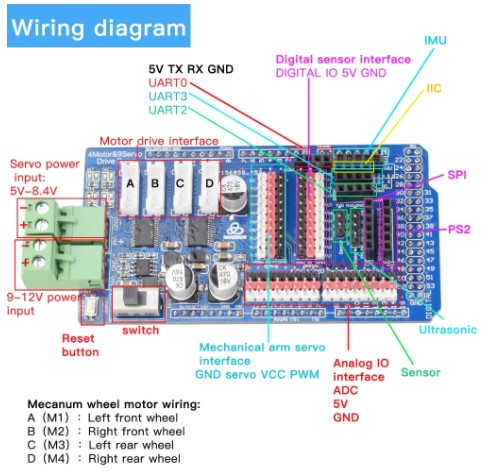
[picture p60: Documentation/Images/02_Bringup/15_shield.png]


- Verify the Pin number of encoders, PWM and DIR in config.h and encoder.h files



Graphically we have designed a **Closed loop PID CD-motor speed control**:

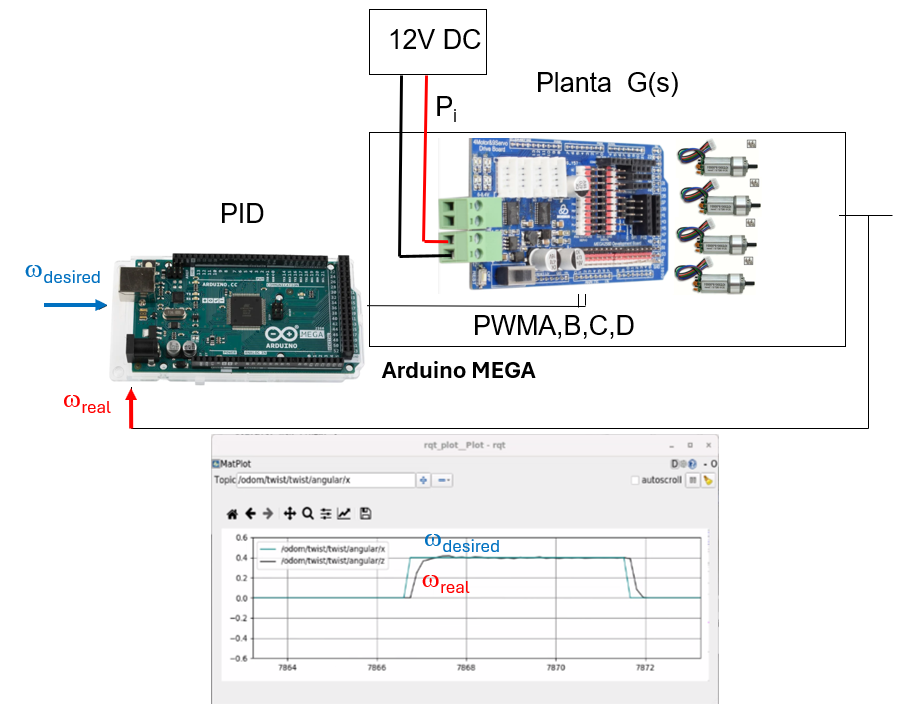
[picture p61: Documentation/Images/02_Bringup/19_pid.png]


Each wheel is turning at a precise speed defined by the inverse kinematics. The speed dynamics and steady state value is ensured by the designed PID closed loop.

### **Final bringup launch file**

We have created a "rubot_bringup_hw_arduino.launch" file to setup the rUBot_mecanum.

To launch the bringup **arduino based driver**, the instruction is:
```shell
roslaunch rubot_mecanum_description rubot_bringup_hw_arduino.launch
```
Graphically we have this structure:

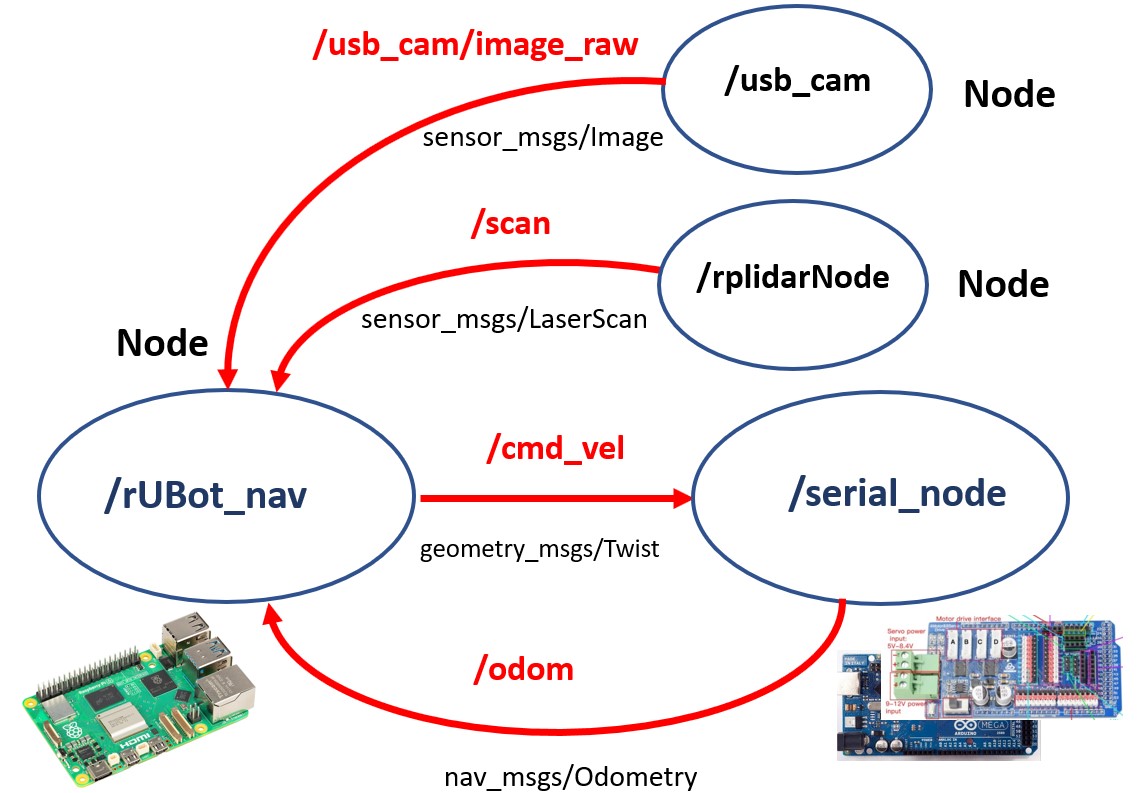
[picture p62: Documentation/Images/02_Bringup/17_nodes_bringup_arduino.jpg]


**Important!:** You have not to execute the rubot_bringup_hw_arduino.launch on the robot. There is a service that executes this bringup on boot!

### **Lab Activity: Lidar test**

The objectives of this activity are:
- Put your robot inside a real world
- Launch the rubot_lidar_test.launch file and verify the number of laser beams. 
- Create a new **rubot_lidar_test_custom.launch** and **rubot_lidar_test_custom.py**, including a laser_factor variable as beams/deg.
- Verify the Lidar is able to identify correctly the obstacles in each angle orientation!

Upload a zip file including:
- picture containing:
  - rviz screen where you can see the lidar distances
  - terminal running the "rubot_lidar_test_custom.launch" with distances readings
- the rubot_lidar_test_custom.py

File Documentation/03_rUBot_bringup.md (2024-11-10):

# **rUBot mecanum Bringup**

The objectives of this chapter are:
- Create a robot model of our rUBot mecanum
- Create a world model of the virtual environment
- Bringup the robot in virtual environment
- Bringup the real robot.

The rUBot mecanum robot we will work is represented in the picture:


**Bibliography:**
- https://bitbucket.org/theconstructcore/workspace/projects/PS

## **1. rUBot mecanum model generation**

First of all, we have created the "rubot_mecanum_description" package where we have created the rUBot model. 

In case you want to create it from scratch, type:
```shell
cd /home/user/rubot_mecanum_ws/src
catkin_create_pkg rubot_mecanum_description rospy
cd ..
catkin_make
```

### **1.1. Model design**

The geometrical definition of our rUBot is graphically described by:


The different elements (named **links**) are:
- base_link
- wheels
- camera
- base_scan

These elements are connected each-other by **joints**:
- base_link_joint
- wheel_joint
- joint_camera
- scan_joint

Some of these links have a speciffic **functionalities**:
- wheels: perform a robot movement according to a Mecanum-drive kinematics
- camera: view front images
- base_scan: detect obstacle distances in 360º around the robot

To create our robot model, we use **URDF files** (Unified Robot Description Format). URDF file is an XML format file for representing a robot model.(http://wiki.ros.org/urdf/Tutorials)

The general structure of a robot urdf model is based on:
- Links and joints: for the geometrical structure
- Gazebo plugins: for the functionalities

The urdf file structure is:
```xml
<?xml version="1.0" encoding="utf-8"?>
<robot name="rubot">
  <link name="base_link">
  ...
  </link>
  <joint name="base_link_joint" type="fixed">
  ...
  </joint>
  <gazebo>
    <plugin name="Mecanum_controller" filename="libgazebo_ros_planar_move.so">
    ...
    </plugin>
  </gazebo>
  <gazebo reference="upper_left_wheel">
  ...
  </gazebo>
</robot>
```

We have created 2 folders for model description:
- URDF: folder where different URDF models are located. In our case rubot.urdf
- meshes: folder where 3D body models in stl format are located. We will have rubot folder.

As we have explained above, main parts of URDF model are:
- links: diferent bodies/plastic elements
- joints: connection between 2 links 
- sensors & actuators plugins (2D camera, LIDAR and 4-wheels mecanum-drive)

The **link definition** contains:
- visual properties: the origin, geometry and material
- collision properties: the origin and geomnetry
- inertial properties: the origin, mass and inertia matrix

The **joint definition** contains:
- joint Type (fixed, continuous)
- parent and child frames
- origin frame
- rotation axis

In the case or upper left wheel link:
```xml
<!-- upper_left_wheel -->
  <link name="upper_left_wheel">
    <visual>
      <origin rpy="0 0 0" xyz="0 0 0"/>
      <geometry>
        <mesh filename="package://rubot_mecanum_description/meshes/rubot/upper_left_wheel.stl" scale="0.001 0.001 0.001"/>
      </geometry>
      <material name="light_grey"/>
    </visual>
    <collision>
      <origin rpy="-1.57 0 0" xyz="0 0 0"/>
      <geometry>
        <cylinder length="0.03" radius="0.05"/>
      </geometry>
    </collision>
    <inertial>
      <origin rpy="-1.57 0 0" xyz="0.0 0.0 0.0"/>
      <mass value="0.2"/>
      <inertia ixx="0.000166" ixy="0" ixz="0" iyy="0.000303" iyz="0" izz="0.000166"/>
    </inertial>
  </link>
  <joint name="upper_left_wheel_joint" type="continuous">
    <origin rpy="0 0 0" xyz="0.07 0.1 0"/>
    <parent link="base_link"/>
    <child link="upper_left_wheel"/>
    <axis xyz="0 1 0"/>
  </joint>
```
> Be careful with base_link:
>
> The inertia matrix can be analytically calculated with the mass and geometry. Be sure the mass is consistent and the inertia Ixx,Iyy and Izz are high enough to avoid underired drift movements. Consider the Inertia matrix you can generate using the **urdf_inertial_calculator.py** program file you have in "Documentation/files/Doc/Robot_Models/URDF_inertial".

The rUBot model includes different **sensors and actuators**:

The full model contains also information about the sensor and actuator controllers using specific **Gazebo plugins** (http://gazebosim.org/tutorials?tut=ros_gzplugins#Tutorial:UsingGazebopluginswithROS). 

Gazebo plugins give your URDF models greater functionality and compatiblility with ROS messages and service calls for sensor output and motor input. 

These plugins can be referenced through a URDF file, and to insert them in the URDF file, you have to follow the sintax:

**2D-camera Sensor**:

The two-dimensional camera sensor corresponds to the USB real camera. 

This camera obtains 2D images in the front and is simulated in URDF model as:
- link with the visual, collision and inertial properties
- joint of fixed type
- Gazebo plugin as a sort of "driver" to simulate the real behaviour

Review the joint and link definition in URDF model.

The used Gazebo plugin is:

```xml
  <!-- 2D Camera controller -->
  <gazebo reference="camera">
    <sensor name="camera1" type="camera">
      <update_rate>30.0</update_rate>
      <camera name="front">
        <horizontal_fov>1.3962634</horizontal_fov>
        <image>
          <width>800</width>
          <height>800</height>
          <format>R8G8B8</format>
        </image>
        <clip>
          <near>0.02</near>
          <far>300</far>
        </clip>
      </camera>
      <plugin filename="libgazebo_ros_camera.so" name="camera_controller">
        <alwaysOn>true</alwaysOn>
        <visualize>true</visualize>
        <cameraName>rubot/camera1</cameraName>
        <imageTopicName>image_raw</imageTopicName>
        <cameraInfoTopicName>camera_info</cameraInfoTopicName>
        <frameName>camera</frameName>
        <hackBaseline>0.07</hackBaseline>
        <distortionK1>0.0</distortionK1>
        <distortionK2>0.0</distortionK2>
        <distortionK3>0.0</distortionK3>
        <distortionT1>0.0</distortionT1>
        <distortionT2>0.0</distortionT2>
      </plugin>
    </sensor>
  </gazebo>
  ```
>To view the camera image you can:
> - add the line in the plugin 
> ```xml
><visualize>true</visualize>"
> ```
> - use rviz
> - type rqt in a terminal and select Plugins->Visualization->Image View
>
>Alternativelly with false in plugin, you can allways call the image typing in a new terminal:
>```shell
>rqt image view
>```

**RPlidar sensor**

A Lidar sensors is  device that is able to measure the obstacle distances at 360º around the robot. 

He is sending 720 laser beams (2 beams/degree) and measures the distance each laser beam finds an obstacle. He is able to measure from 12cm to 10m. The used Lidar sensor is a 360º RPLidar A1M8 (https://www.robotshop.com/es/es/rplidar-a1m8-kit-desarrollo-escaner-laser-360-grados.html)

This lidar is simulated in URDF model as:
- link with the visual, collision and inertial properties
- joint of fixed type
- Gazebo plugin as a sort of "driver" to simulate the real behaviour

 Review the joint and link definition in URDF model.
> Note that rpLIDAR is mounted at 180º and you need to turn the link model and the joint to reflect this in the URDF model.



The gazebo plugin we have used is:
```xml
  <!-- Laser Distance Sensor RPLIDAR controller-->
  <gazebo reference="base_scan">
    <sensor name="lds_lfcd_sensor" type="ray">
      <pose>0 0 0 0 0 0</pose>
      <visualize>true</visualize>
      <update_rate>5</update_rate>
      <ray>
        <scan>
          <horizontal>
            <samples>720</samples>
            <resolution>1</resolution>
            <min_angle>0.0</min_angle>
            <max_angle>6.28319</max_angle>
          </horizontal>
        </scan>
        <range>
          <min>0.12</min>
          <max>10</max>
          <resolution>0.015</resolution>
        </range>
        <noise>
          <type>gaussian</type>
          <!-- Noise parameters based on published spec for YDLIDAR X4
              is 1.5% at half range 4m (= 60mm, "+-160mm" accuracy at max. range 8m).
              A mean of 0.0m and stddev of 0.020m will put 99.7% of samples
              within 0.16m of the true reading. -->
          <mean>0.0</mean>
          <stddev>0.02</stddev>
        </noise>
      </ray>
      <plugin filename="libgazebo_ros_laser.so" name="gazebo_ros_lds_lfcd_controller">
        <!-- topicName>/gopigo/scan</topicName -->
        <topicName>scan</topicName>
        <frameName>base_scan</frameName>
      </plugin>
    </sensor>
  </gazebo>
```
>To view the LIDAR rays be sure to add 
> ```xml
><visualize>true</visualize>"
> ```
> or use rviz

It is important to note that:
- the number of points of real RPLidar depends on Lidar model (you will need tot test it first)
- the number of points of simulated Lidar is selected to 720

**Actuator**:

The rUBot_mecanum contains a "Mecanum drive actuator" based on:
- 4 wheels driven by a DC servomotor 
- with speciffic Kinematic control 
- able to move the robot in x and y directions
- and able to obtain the Odometry information

Gazebo plugin is a sort of "driver" to simulate the Kinematics of our rUBot_mecanum.

The **rUBot_mecanum kinematics** describes the relationship between the robot wheel speeds and the robot velocity. We have to distinguish:
- **Forward kinematics**: obtains the robot velocity (linear and angular in /cmd_vel) and POSE (odometry) for speciffic robot wheel speeds
- **Inverse kinematics**: obtains the robot wheels speeds for a desired robot velocity (linear and angular in /cmd_vel)

The different movements the Mecanum robot is able to perform are:



This kinematics and odometry calculations are described in the "libgazebo_ros_planar_move.so" file and the URDF model will contain the specific gazebo plugin.

This driver is the "Planar Move Plugin" and is described in Gazebo tutorials: http://gazebosim.org/tutorials?tut=ros_gzplugins#AddingaModelPlugin

```xml
  <!-- Mecanum drive controller -->
  <gazebo>
    <plugin name="Mecanum_controller" filename="libgazebo_ros_planar_move.so">
      <commandTopic>cmd_vel</commandTopic>
      <odometryTopic>odom</odometryTopic>
      <odometryFrame>odom</odometryFrame>
      <odometryRate>50.0</odometryRate>
      <robotBaseFrame>base_footprint</robotBaseFrame>
    </plugin>
  </gazebo>
  ```

### **1.2. ROS visualization Tools**

ROS has two powerfull visualization tools:
- RVIZ: used to visualize the robot model and the messages published in the different topics
- Gazebo: is a physical simulator 

**RVIZ**

We will first use RVIZ to check that the model is properly built. 

RViz only represents the robot visual features. You have available all the options to check every aspect of the appearance of the model.

We use a specific "display.launch" launch file where we specify the robot model we want to open in rviz with a configuration specified in "urdf.rviz":
```xml
<launch>
  <param name="robot_description" textfile="$(find rubot_mecanum_description)/urdf/rubot.urdf" />
  <node name="joint_state_publisher" pkg="joint_state_publisher" type="joint_state_publisher" />

  <node name="robot_state_publisher" pkg="robot_state_publisher" type="robot_state_publisher" />
  <node name="rviz" pkg="rviz" type="rviz" args="-d $(find rubot_mecanum_description)/rviz/urdf_final.rviz" />
</launch>
```
```shell
roslaunch rubot_mecanum_description rubot_rviz.launch
```


> Colors in rviz: 
>- are defined at the beginning
>- Ensure the "visual" link properties have color "name"
```xml
<robot name="rubot">
  <material name="yellow">
    <color rgba="0.8 0.8 0.0 1.0"/>
  </material>

  ...

    <link name="base_link">
    <visual>
      <origin rpy="0 0 0" xyz="0 0 0"/>
      <geometry>
        <mesh filename="package://rubot_mecanum_description/meshes/rubot/base_link.stl" scale="0.001 0.001 0.001"/>
      </geometry>
      <material name="yellow"/>
    </visual>
```
**Gazebo**

In robotics research, always before working with a real robot, we simulate the robot behaviour in a virtual environment close to the real one. **Gazebo** is an open source 3D robotics simulator and includes an ODE physics engine and OpenGL rendering, and supports code integration for closed-loop control in robot drives. This is sensor simulation and actuator control.

We will create a new rubot_gazebo.launch file to spawn the robot in an empty world:
```xml
<launch>
  <!-- Define the needed parameters -->
  <arg name="model" default="rubot.urdf" />

  <include file="$(find gazebo_ros)/launch/empty_world.launch"/>
  <!-- Spawn the robot -->
  <!-- Robot URDF definition -->
    <param name="robot_description" textfile="$(find rubot_mecanum_description)/urdf/$(arg model)"/>
  <node name="spawn_model" pkg="gazebo_ros" type="spawn_model"
    args="-urdf -model rUBot -param robot_description"/>
</launch>
```
Open a new terminal and launch this file:
```shell
roslaunch rubot_mecanum_description rubot_gazebo.launch
roslaunch rubot_mecanum_description rubot_rviz.launch
```


You will see in Rviz the camera is receiving now images!
> Colors in gazebo: 
>- are defined at the end of urdf file:
```xml
<!-- Gazebo colors have to be specified here with predefined Gazebo colors -->
  <gazebo reference="base_link">
    <material>Gazebo/Yellow</material>
  </gazebo>
```
You can create a very **simple world** "rubot.world" using gazebo:

- Maintain the Gazebo and RVIZ screens opened
- add some objects in the empty world

Now in RVIZ you will see the objects with the USB camera and Lidar



You can see the nodes and topics generated using rqt_graph


> To see the frames you have to add TF in rviz

>Carefull:
- Perhaps is needed to setup your Keys again:
  ```shell
  curl -s https://raw.githubusercontent.com/ros/rosdistro/master/ros.asc | sudo apt-key add -
  sudo apt get update
  sudo apt get upgrade
  ```
- To close the Gazebo is better to type in a new terminal:
  ```shell
  pkill gzserver && pkill gzclient
  ```

## **2. Design the project world**

Here we have first to design the project world, for exemple a maze from where our rUBot mecanum has to navigate autonomously.

There is a very useful and simple tool to design a proper world: "**Building editor**" in gazebo.

Open gazebo as superuser:
```shell
sudo gazebo
```

You can build your world using "Building Editor" in Edit menu



- Save the generated model in a model folder (without extension)
- Close the Builder Editor, modify the model position and add other models to configure your virtual desired world.
- Save the generated world (with extension .world) in the world folder.

Once you finish is better to close the terminal you have work as superuser

#### ***Modify a created world***
- Open a terminal where you have the world you want to modify
- type: sudo gazebo ./test.world (or simply "gazebo test.world")
- make modifications: add some other models, delete previously added models, etc.
- save your world in a world directory
- close gazebo and the terminal
#### **Create world with model parts**
You can create model parts like walls of 60cm or 90cm or 120cm with a geometry and color, using building editor. These parts can be saved:
- in ~/.gazebo/models/ (this is the default folder)
- in speciffic folder in your package (i.e. rUBot_mecanum_ws/src/rubot_mecanum_description/models). In this case, to add the path in Gazebo, add this line in .bashrc file:
  ```xml
  export GAZEBO_MODEL_PATH=/home/user/rUBot_mecanum_ws/src/rubot_mecanum_description/models:$GAZEBO_MODEL_PATH
  ```
- When a model is created with "Building Editor", this path is saved in gazebo environment and you can use it in the future.
- You can allways select "Add folder path" in "insert" gazebo menu tab, and select the models folder you have created in your project ws 

You will have acces in gazebo insert section. Then you can construct your world adding parts.

This is an exemple:


## **3. Bringup the rUBot in Virtual environment**

The first step in robotics is to bringup the rUBot mecanum robot in our generated virtual world. This means:
- Open Gazebo with the designed virtual world
- spawn our robot in the designed virtual world 
- and open Rviz to see the topic messages.

This is defined in "rubot_bringup_sw.launch" file. 
``` shell
roslaunch rubot_mecanum_description rubot_bringup_sw.launch
```


>Careful:
- we have included in launch file: gazebo rubot spawn and rviz visualization 
- Verify in rviz you have in fixed frame the "odom" frame

Now we are ready to control our robot in this virtual environment!

**Activity: rUBot Bringup SW**

The objective of this activity is to spawn our custom rUBot in a virtual world.

You will have to:
- Design a custom rUBot model corresponding to the real rUBot_mecanum (rubot_custom.urdf), with:
  - Customized model colors (rviz and gazebo)
  - Add a 3D-part on top with a fixed joint
  - Modify the "base_scan" link and joint to take into account the lidar orientation in our robot
- Design a custom virtual world using the wooden model parts

To verify the final bringup, create a new "rubot_bringup_sw_custom.launch" file with your rubot_custom.urdf and the world you have created:
```shell
roslaunch rubot_mecanum_description rubot_bringup_sw_custom.launch
```


Upload a zip file with:
- Picture with gazebo and rviz obtained with your custom rubot model and designed world
- file: "rubot_custom.urdf"
- file: "rubot_bringup_sw_custom.launch"

## **4. Bringup the real robot**

The rUBot Mecanum real hardware is based on:
- Robot base structure with 4 Mecanum wheels driven by DC-servomotors
- 2D-Camera to generate front images
- Lidar for Navigation with obstacle avoidance
- Arduino Mega with custom Shield: to control the 4 Mecanum Wheels (and other sensors onboard in function of the application)
- Raspberrypi4b Computer on-board: for high level control in ROS environment. He will also control directly the usb-camera and the Lidar.

To Bingup our real robot we have to:
 
- Launch the "Mecanum-drive control" module for servomotor actuators for the 4 mecanum wheels
- Launch the RPlidar distance sensor
- Launch the usb camera sensor



### **4.1. Launch the "Mecanum-drive control" module**

The 4 mecanum wheels can be controlled by:
- Arduino Mega based control shield
- Raspberrypi4b custom shield

#### **4.1.2 Arduino Mega based control shield**

The 4 mecanum wheels will be controlled by a Arduino Mega shield based control board.

Let's see some important characteristics:
- You need to install Encoder.h lib: https://www.arduino.cc/reference/en/libraries/encoder/
- Verify the Motor connections order



- Verify the Shield schematics for the A,B,C,D bus-connectors



- Verify the Pin number of encoders, PWM and DIR in config.h and encoder.h files



Graphically we have designed a **Closed loop PID CD-motor speed control**:



Each wheel is turning at a precise speed defined by the inverse kinematics. The speed dynamics and steady state value is ensured by the designed PID closed loop.

To enable this control mode shield you have to include in the bringup file:
````shell
<!-- launch rUBot mecanum  -->
    <node name="serial_node" pkg="rosserial_python" type="serial_node.py">
      <param name="port" type="string" value="/dev/ttyACM0"/>
      <param name="baud" type="int" value="57600"/>
    </node>
````
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

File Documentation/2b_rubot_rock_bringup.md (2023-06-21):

# **rUBot Mecanum Hardware bringup**
The hardware bringup file will contain:
- launch the rUBot node in Arduino-Mega board
- launch the LIDAR node
- launch the usb_cam node

Graphically, the final node structure will be:
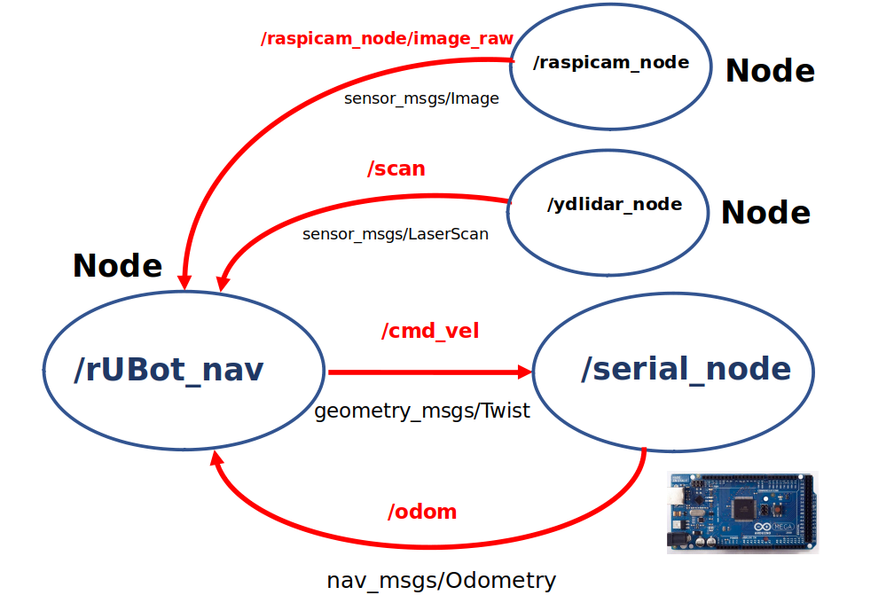
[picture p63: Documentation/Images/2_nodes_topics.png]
Getting Started


The bringup launch file will prepare the rUBot to comunicate with /rUBot_nav node for specific control actions.

## **1. Launch rUBot node**

To bringup we need to run the driver designed for rubot_mecanum robot. The driver is in fact an arduino program that controls:

- The kinematics of the 4 mecanum wheels to apply the twist message in /cmd_vel topic
- The encoders to obtain the odometry
- Read the IMU orientation values
- interface with all the other sensors/actuators connected to arduino-mega board

The "rubot_mecanum.ino" arduino program is located on /Documentation/files/arduino/ folder
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

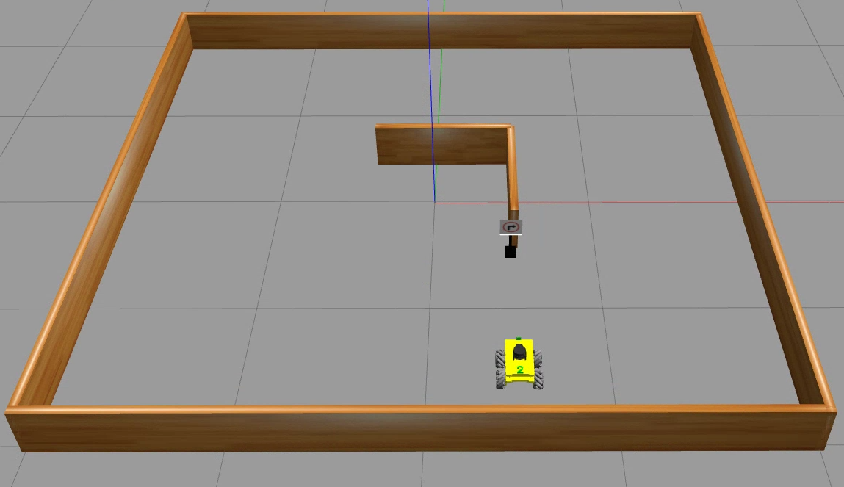
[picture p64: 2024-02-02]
Documentation/Images/05_Projects/project3_bringup.png

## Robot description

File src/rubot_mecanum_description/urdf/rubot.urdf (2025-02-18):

<?xml version="1.0" encoding="utf-8"?>
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
<robot name="rubot">
  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
  <link name="base_footprint"/>
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
  <joint name="base_link_joint" type="fixed">
    <origin rpy="0 0 0" xyz="0 0 0"/>
    <parent link="base_footprint"/>
    <child link="base_link"/>
  </joint>
  <link name="base_link">
    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
    <inertial>
      <origin rpy="0 0 0" xyz="0 0 0"/>
      <mass value="5"/>
      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
    </inertial>
  </link>
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
  <joint name="upper_left_wheel_joint" type="continuous">
    <origin rpy="0 0 0" xyz="0.07 0.1 0"/>
    <parent link="base_link"/>
    <child link="upper_left_wheel"/>
    <axis xyz="0 1 0"/>
  </joint>
  <link name="upper_left_wheel">
    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
    <inertial>
      <mass value="0.2"/>
      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
    </inertial>
  </link>
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
  <joint name="lower_left_wheel_joint" type="continuous">
    <origin rpy="0 0 0" xyz="-0.085 0.1 0"/>
    <parent link="base_link"/>
    <child link="lower_left_wheel"/>
    <axis xyz="0 1 0"/>
  </joint>
  <link name="lower_left_wheel">
    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
    <inertial>
      <mass value="0.2"/>
      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
    </inertial>
  </link>
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
  <joint name="upper_right_wheel_joint" type="continuous">
    <origin rpy="0 0 3.14" xyz="0.07 -0.1 0"/>
    <parent link="base_link"/>
    <child link="upper_right_wheel"/>
    <axis xyz="0 -1 0"/>
  </joint>
  <link name="upper_right_wheel">
    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
    <inertial>
      <mass value="0.2"/>
      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
    </inertial>
  </link>
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
  <joint name="lower_right_wheel_joint" type="continuous">
    <origin rpy="0 0 3.14" xyz="-0.085 -0.1 0"/>
    <parent link="base_link"/>
    <child link="lower_right_wheel"/>
    <axis xyz="0 -1 0"/>
  </joint>
  <link name="lower_right_wheel">
    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
    <inertial>
      <mass value="0.2"/>
      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
    </inertial>
  </link>
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
  <joint name="joint_camera" type="fixed">
    <origin rpy="0 0 0" xyz="0.120 0.0 0.09"/>
    <parent link="base_link"/>
    <child link="camera"/>
    <axis xyz="0 1 0"/>
  </joint>
  <link name="camera">
    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
    <inertial>
      <origin rpy="0 1.570795 0" xyz="0 0 0"/>
      <mass value="0.01"/>
      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
    </inertial>
  </link>
  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
  <link name="base_scan">
    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
    <inertial>
      <origin rpy="0 0 0" xyz="0 0 0.4"/>
      <mass value="0.05"/>
      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
    </inertial>
  </link>
  <joint name="scan_joint" type="fixed">
    <axis xyz="0 0 1"/>
    <origin rpy="0 0 0" xyz="0 0 0.15"/>
    <parent link="base_link"/>
    <child link="base_scan"/>
  </joint>
  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
  <joint name="joint_part" type="fixed">
    <origin rpy="0 0 0" xyz="-0.10 0.0 0.09"/>
    <parent link="base_link"/>
    <child link="part"/>
  </joint>
  <link name="part">
    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
    <inertial>
      <mass value="0.01"/>
      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
    </inertial>
  </link>
  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
</robot>

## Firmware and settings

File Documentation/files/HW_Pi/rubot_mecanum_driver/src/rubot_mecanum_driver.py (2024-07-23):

#!/usr/bin/env python3


import pigpio
import time as t
import rospy
import math
from geometry_msgs.msg import Twist, TransformStamped
from nav_msgs.msg import Odometry
from std_msgs.msg import Bool
from tf.transformations import quaternion_from_euler
import threading
import tf2_ros
from rubot_mecanum_library import Encoder, MPID, DCMotorController 

class rubot_drive():
    def __init__(self):
        #Robot Constant Parameter definition
        self.xn = 0.082 
        self.yn = 0.105 
        self.r = 0.04 # Other robot 0.025
        self.K = abs(self.xn) + abs(self.yn) - 0.02
        self.max_rmp = 330
        self.resolution = 2 * math.pi * self.r / 1320 # 1440
        
        #Odometry Variables
        self.vx = 0
        self.vy = 0
        self.w = 0
        self.theta = 0
        self.x = 0
        self.y = 0
        self.vxi = 0
        self.vyi = 0
        self.wi = 0
        
        # PID
        self.kp = 0.2 #0.4
        self.kd = 0.4 #0.8
        self.ki = 0.25 #0.35
        
        #Encoder position variables 
        self.position1 = 0
        self.position2 = 0
        self.position3 = 0
        self.position4 = 0

        # Initiate pigpio
        self.pi = pigpio.pi()
        
        # Motor and Encoder Pin distribution and configuration
        # Motor1 -----FRONT-LEFT Wheel-------- 4
        self.EnA = Encoder(self.pi,24, 25,self.callback1)
        self.PIDA = MPID(self.kp, self.ki, self.kd, True,self.r,self.resolution,self.max_rmp)
        self.MotorA = DCMotorController(self.pi,13, 27, 22, 10)
        
     
        # Motor2 -----FRONT-RIGHT Wheel-------- 3
        self.EnB = Encoder(self.pi,23,15,self.callback2)
        self.PIDB = MPID(self.kp, self.ki, self.kd, False,self.r,self.resolution,self.max_rmp)
        self.MotorB = DCMotorController(self.pi,19, 4, 17, 10)        

        
        # Motor3 -----BACK-LEFT Wheel--------
        self.EnC = Encoder(self.pi,16, 20,self.callback3) #8 i 16
        self.PIDC = MPID(self.kp, self.ki, self.kd, True,self.r,self.resolution,self.max_rmp)
        self.MotorC = DCMotorController(self.pi,12,5,6, 10) #12,6,26, 10
        

        # Motor4 -----BACK-RIGHT Wheel--------
        self.EnD = Encoder(self.pi,26, 21,self.callback4) #21,20
        self.PIDD = MPID(self.kp, self.ki, self.kd, True,self.r,self.resolution,self.max_rmp)
        self.MotorD = DCMotorController(self.pi,18, 11, 9, 10)#18, 5, 11, 10
        
        
       
        # ROS-related variables,msg and node creation
        rospy.init_node('dc_motor_controller')
        self.odom_pub = rospy.Publisher('odom', Odometry, queue_size=10)
        rospy.Subscriber('/cmd_vel', Twist, self.speed_callback)
        rospy.Subscriber('reset_odom', Bool, self.reset_odom_callback)
        self.broadcaster = tf2_ros.TransformBroadcaster()
        
        #Sampling and Time control variables
        self.ctrlrate = 1
        self.lastctrl = rospy.Time.now()
        self.num = 0
        self.sample = 1 # 2

	#Encoder Callback funtions
    def callback1(self,pos):
        self.position1 += pos
    def callback2(self,pos):
        self.position2 += pos
    def callback3(self,pos):
        self.position3 += pos
    def callback4(self,pos):
        self.position4 += pos
        
        
    def rpm2pwm(self, rpm):
        return int(rpm / self.max_rmp * 255)
    def speed2rpm(self, spd):
        return int( 30.0 * spd / (self.r * math.pi))
    def speed2pwm(self, spd):
        return self.rpm2pwm(self.speed2rpm(spd))
        
    def InverseKinematic(self, vx, vy, omega):
        pwmA = self.speed2pwm((vx - vy - self.K * omega))
        pwmB = self.speed2pwm((vx + vy + self.K * omega))
        pwmC = self.speed2pwm((vx + vy - self.K * omega))
        pwmD = self.speed2pwm((vx - vy + self.K * omega))
        return pwmA, pwmB, pwmC, pwmD

    def ForwardKinematic(self, wA, wB, wC, wD):
        vx = self.r / 4 * (wA + wB + wC + wD)
        vy = self.r / 4 * (-wA + wB + wC - wD)
        omega = self.r / (4 * self.K) * (-wA + wB - wC + wD)
        return vx, vy, omega

    # Funtion that saves the values of the message published in /cmd_vel
    def speed_callback(self, msg):
        self.vx = msg.linear.x
        self.vy = msg.linear.y
        self.w =  msg.angular.z
        self.lastctrl = rospy.Time.now()
    # Funtion that resets the odometry values
    def reset_odom_callback(self,msg):
        if(msg.data):
            self.x = 0
            self.y = 0
            self.theta = 0
            self.num = 0
    #Shutdown Funtion
    def shutdown(self):
        self.MotorA.speed(self.pi,0)
        self.MotorB.speed(self.pi,0)
        self.MotorC.speed(self.pi,0)
        self.MotorD.speed(self.pi,0)
    
    #motor PID management thread
    def pid_thread(self):
        rate = rospy.Rate(10)  # Frecuencia de actualización de 10 Hz
        self.duty1 = 0        
        self.duty2 = 0
        self.duty3 = 0 
        self.duty4 = 0 
        self.constant = 0    
        wa = 0
        wb = 0
        wc = 0
        wd = 0    
        while not rospy.is_shutdown():
        	
            self.pwma, self.pwmb, self.pwmc, self.pwmd = self.InverseKinematic(self.vx, self.vy, self.w)
            

            self.PIDA.tic(self.position1)
            self.duty1 = self.PIDA.set_pwm(self.pwma)
            self.MotorA.speed(self.pi,self.duty1)
            wa = self.PIDA.getWheelRotatialSpeed()
            self.PIDA.toc()
            
            
            
            self.PIDB.tic(self.position2)
            self.duty2 = self.PIDB.set_pwm(self.pwmb)
            self.MotorB.speed(self.pi,self.duty2)
            wb = self.PIDB.getWheelRotatialSpeed()
            self.PIDB.toc()
     
            
            
            self.PIDC.tic(self.position3)
            self.duty3 = self.PIDC.set_pwm(self.pwmc)
            self.MotorC.speed(self.pi,self.duty3)
            wc = (self.PIDC.getWheelRotatialSpeed())  
            self.PIDC.toc()
            
           
          
            self.PIDD.tic(self.position4)
            self.duty4 = self.PIDD.set_pwm(self.pwmd)
            self.MotorD.speed(self.pi,self.duty4)
            wd = self.PIDD.getWheelRotatialSpeed()
            self.PIDD.toc()
   
            #Odometry
            self.vxi, self.vyi, self.wi = self.ForwardKinematic(wa, wb, wc, wd)
            dt = self.PIDA.get_deltaT()
            self.theta += self.wi * (dt*1.175)  
            if self.theta > 2 * math.pi:
                self.theta -= 2 * math.pi
            elif self.theta < 0:
                self.theta += 2 * math.pi
            self.x += self.vxi * math.cos(self.theta) * dt - self.vyi * math.sin(self.theta) * dt  
            self.y += self.vxi * math.sin(self.theta) * dt + self.vyi * math.cos(self.theta) * dt 
            
            if abs(wa) > 0.15:
                self.num += 1
           
            rate.sleep()
 
    def open_thread(self):
        rate1 = rospy.Rate(12)  # Frecuencia de actualización de 10 Hz
        self.duty1 = 0        
        self.duty2 = 0
        self.duty3 = 0 
        self.duty4 = 0  
        self.constant = 0  
        wa = 0
        wb = 0
        wc = 0
        wd = 0    
        while not rospy.is_shutdown():
        	
            self.pwma, self.pwmb, self.pwmc, self.pwmd = self.InverseKinematic(self.vx, self.vy, self.w)
    

            self.PIDA.tic(self.position1)
            self.duty1 = self.PIDA.set_pwm(self.pwma)
            self.MotorA.speed(self.pi,self.pwma)
            wa += self.PIDA.getWheelRotatialSpeed()
            self.PIDA.toc()

            
            self.PIDB.tic(self.position2)
            self.duty2 = self.PIDB.set_pwm(self.pwmb)
            self.MotorB.speed(self.pi,self.pwmb)
            wb += self.PIDB.getWheelRotatialSpeed()
            self.PIDB.toc()
            
            self.PIDC.tic(self.position3)
            self.duty3 = self.PIDC.set_pwm(self.pwmc)
            self.MotorC.speed(self.pi,self.pwmc)
            wc += self.PIDC.getWheelRotatialSpeed() 
            self.PIDC.toc()
          
           
            self.PIDD.tic(self.position4)
            self.duty4 = self.PIDD.set_pwm(self.pwmd)
            self.MotorD.speed(self.pi,self.pwmd)
            wd += self.PIDD.getWheelRotatialSpeed()
            self.PIDD.toc()

            if self.constant == self.sample:
                self.constant = 0
                self.vxi, self.vyi, self.wi = self.ForwardKinematic(wa/self.sample, wb/self.sample, wc/self.sample, wd/self.sample)
                """
                print("MotorA dut: " + str(self.duty1))
                print("MotorB dut: " + str(self.duty2))
                print("MotorC dut: " + str(self.duty3))
                print("MotorD dut: " + str(self.duty4))
                
                print("WA: " + str(wa/self.sample))
                print("WB: " + str(wb/self.sample))
                print("WC: " + str(wc/self.sample))
                print("WD: " + str(wd/self.sample))
                print("Vx: " + str(self.vxi))
                print("Vy: " + str(self.vyi))
                print("W: " + str(self.wi))
                print("N: " +str(self.num))
                
                print("posA: " + str(self.position1))
                print("posD: " + str(self.position4))
                
                print("PWMA: " + str(self.position1))
                print("PWMB: " + str(self.position2))
                print("PWMC: " + str(self.position3))
                print("PWMD: " + str(self.position4))
                """
                # Update odometry and publish here
                dt = self.PIDA.get_deltaT()
                self.theta += self.wi * dt * self.sample
                if self.theta > 2 * math.pi:
                    self.theta -= 2 * math.pi
                elif self.theta < 0:
                    self.theta += 2 * math.pi
                self.x += self.vxi * math.cos(self.theta) * dt - self.vyi * math.sin(self.theta) * dt 
                self.y += self.vxi * math.sin(self.theta) * dt + self.vyi * math.cos(self.theta) * dt 
                if abs(self.wi) > 0.001:
                    self.num += 1
                wa = 0
                wb = 0
                wc = 0
                wd = 0
                
            self.constant += 1
            
            rate1.sleep()
            
    #Odom publisher thread    
    def publishOdom_thread(self):
        rate = rospy.Rate(25)  # Frecuencia de actualización de 10 Hz

        while not rospy.is_shutdown():
            quaternion = quaternion_from_euler(0, 0, self.theta)
            #print("PWM applied: " + str(self.pwma))
            t = TransformStamped()
            t.header.stamp = rospy.Time.now()
            t.header.frame_id = "odom"
            t.child_frame_id = "base_footprint"
            t.transform.translation.x = self.x 
            t.transform.translation.y = self.y 
            t.transform.rotation.x = quaternion[0]
            t.transform.rotation.y = quaternion[1]
            t.transform.rotation.z = quaternion[2]
            t.transform.rotation.w = quaternion[3]
            self.broadcaster.sendTransform(t)

            odom = Odometry()
            odom.header.stamp = rospy.Time.now()
            odom.header.frame_id = "odom"
            odom.child_frame_id = "base_footprint"
            odom.pose.pose.position.x = self.x 
            odom.pose.pose.position.y = self.y 
            odom.pose.pose.orientation.x = quaternion[0]
            odom.pose.pose.orientation.y = quaternion[1]
            odom.pose.pose.orientation.z = quaternion[2]
            odom.pose.pose.orientation.w = quaternion[3]
            odom.twist.twist.linear.x = self.vxi
            odom.twist.twist.linear.y = self.vyi
            odom.twist.twist.linear.z = self.num # Data for debugging
            odom.twist.twist.angular.x = self.w # Data for debugging
            odom.twist.twist.angular.y = self.theta * 180 / math.pi # Data for debugging
            odom.twist.twist.angular.z = self.wi 
            self.odom_pub.publish(odom)

            if (rospy.Time.now() - self.lastctrl).to_sec() > 2.0 / self.ctrlrate:
                self.shutdown()
                self.vx, self.vy, self.w = 0, 0, 0
                self.vxi, self.vyi, self.wi = 0, 0, 0    

            rate.sleep()

    def start(self):
        pid_thread = threading.Thread(target=self.pid_thread)
        publishOdom_thread = threading.Thread(target=self.publishOdom_thread)
        #open_thread = threading.Thread(target=self.open_thread)  
 
        pid_thread.start()
        publishOdom_thread.start()
        #open_thread.start()

        pid_thread.join()
        publishOdom_thread.join()
        #open_thread.join()

if __name__ == '__main__':
    try:
        rUBot1 = rubot_drive()
        rUBot1.start()
        rUBot1.shutdown()
    except rospy.ROSInterruptException or KeyboardInterrupt:
        rUBot1.shutdown()
        pass

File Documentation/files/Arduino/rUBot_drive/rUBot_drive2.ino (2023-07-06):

// Program rUBot mecanum
#include <ros.h>
#include <ros/time.h>
#include <tf/tf.h>
#include <tf/transform_broadcaster.h>
#include <geometry_msgs/Twist.h>
#include <nav_msgs/Odometry.h>
#include<std_msgs/Bool.h>

//#include "src/RoboticsUB.h"
#include "encoder.h"
#include "kinematics.hpp"
#include "motor.h"
#include "pid.hpp"
#include "imu.hpp"

ros::NodeHandle nh;

tf::TransformBroadcaster broadcaster;
geometry_msgs::TransformStamped t;
geometry_msgs::Twist twist;
nav_msgs::Odometry odom;
ros::Publisher odom_pub("odom", &odom);
//ros::Publisher imu_pub("imu",&imu_msg);

// Global Variables
float ctrlrate=1.0;
unsigned long lastctrl;
float x=0,y=0,theta=0;
float vx=0,vy=0,w=0;

// IMU
const int PIN_IMU_INT = 18;
//float *rpw;
//float *q;
// Motors PID
float KP=0.3,KI=0.2,KD=0.2;
MPID PIDA(encA,KP,KI,KD,true);
MPID PIDB(encB,KP,KI,KD,false);
MPID PIDC(encC,KP,KI,KD,true);
MPID PIDD(encD,KP,KI,KD,false);


void cmdVelCb( const geometry_msgs::Twist& twist_msg){
  vx=twist_msg.linear.x;
  vy=twist_msg.linear.y;
  w=twist_msg.angular.z;

  float pwma=0,pwmb=0,pwmc=0,pwmd=0;
  InverseKinematic(vx,vy,w,pwma,pwmb,pwmc,pwmd);
  
  PIDA.tic();PIDB.tic();PIDC.tic();PIDD.tic();
  
  MotorA(PIDA.getPWM(pwma));
  MotorB(PIDB.getPWM(pwmb));
  MotorC(PIDC.getPWM(pwmc));  
  MotorD(PIDD.getPWM(pwmd));
  
  PIDA.toc();PIDB.toc();PIDC.toc();PIDD.toc();

  lastctrl=millis();
}

void resetCb(const std_msgs::Bool& reset){
  if(reset.data){
    x=0.0;y=0.0;theta=0.0;
  }else{
    
  }
}

ros::Subscriber<geometry_msgs::Twist> sub("cmd_vel", cmdVelCb );
ros::Subscriber<std_msgs::Bool> resub("reset_odom", resetCb );


void setup()
{
  //pinMode(PIN_IMU_INT, INPUT_PULLUP);
  //imu.Install();
  
  IO_init();
  PIDA.init();
  PIDB.init();
  PIDC.init();
  PIDD.init();

  nh.initNode();
  broadcaster.init(nh);
  nh.subscribe(sub);
  nh.subscribe(resub);
  nh.advertise(odom_pub);
  //nh.advertise(imu_pub);
  lastctrl=millis();
}

void loop(){
  //float ax,ay,az,gx,gy,gz;
  //delay(10);
  float wA,wB,wC,wD;
  float vxi,vyi,wi;
  
  //float vxi,vyi,omegai;

  PIDA.tic();
  wA=PIDA.getWheelRotatialSpeed();
  PIDA.toc();

  PIDB.tic();
  wB=PIDB.getWheelRotatialSpeed();
  PIDB.toc();

  PIDC.tic();
  wC=PIDC.getWheelRotatialSpeed();
  PIDC.toc();

  PIDD.tic();
  wD=PIDD.getWheelRotatialSpeed();
  PIDD.toc();

  // Twist vector transition
  //ForwardKinematic(wA,wB,wC,wD,vxi,vyi,wi);
  float dt=PIDA.getDeltaT();
  // Odom with transition vxi, vyi
  //x+=vxi*cos(theta)*dt-vyi*sin(theta)*dt;
  //y+=vxi*sin(theta)*dt+vyi*cos(theta)*dt;
  //theta+=omegai*dt;
  //if(theta > 3.14)
  //  theta=-3.14;
  
  // Odom with transition vx, vy
  theta+=w*dt;
  if(theta > 3.14)
    theta=-3.14;
  x+=vx*cos(theta)*dt-vy*sin(theta)*dt;
  y+=vx*sin(theta)*dt+vy*cos(theta)*dt;
  
  t.header.stamp = nh.now();
  t.header.frame_id = "odom";
  t.child_frame_id = "base_footprint";
  t.transform.translation.x = x;
  t.transform.translation.y = y;
  t.transform.rotation = tf::createQuaternionFromYaw(theta);

  broadcaster.sendTransform(t);
  
  odom.header.stamp = nh.now();
  odom.header.frame_id = "odom";
  odom.child_frame_id = "base_footprint";
  odom.pose.pose.position.x = x;
  odom.pose.pose.position.y = y;
  odom.pose.pose.position.z = 0.0;
  odom.pose.pose.orientation =tf::createQuaternionFromYaw(theta);;
  //odom.twist.twist.linear.x = vxi;
  odom.twist.twist.linear.x = vx;
  //odom.twist.twist.linear.y = vyi;
  odom.twist.twist.linear.y = vy;
  //odom.twist.twist.angular.z = omegai;
  odom.twist.twist.angular.z = w;

  odom_pub.publish(&odom);

  // IMU
  //if (digitalRead(PIN_IMU_INT) == HIGH)
  //{
  //  imu.ReadSensor();
  //  q = imu.GetQuaternion();
  //}
  //imu_msg.header.stamp = nh.now();
  //imu_msg.orientation.x = q[0]
  //imu_msg.orientation.y = q[0]
  //imu_msg.orientation.z = q[0]
  //imu_msg.orientation.w = q[0]

  //imu_pub.publish(&imu_msg);
  

  if((millis()-lastctrl)>1000*ctrlrate){
    STOP();
  }
  nh.spinOnce();
 
}

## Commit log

2022-03-07 Commit sin documentation
    [Hybrid.obj, X4.stl, lidar.stl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]
2022-03-07 Documentació del projecte
    [Arduino (Meshed).stl, Arduino_MEGA2560.stl, Arduino_MEGA_Bumper_0003.stl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]
2022-03-07 rubot urdf
    [rubot.urdf]
2022-03-09 Corrections ranges lidar
2022-03-11 Bringup and model
    [rubot0.urdf]
2022-03-16 rubot yd
    [rubot0.urdf]
2022-03-16 arduino program
2022-03-16 Test rp
    [rubot_rp.urdf]
2022-03-16 Change Encoder B M4
2022-03-17 Arduino code
2022-03-18 Odometry arduino
    [PinMap.xlsx]
2022-03-30 Added firsts kinematics tests
2022-05-08 Lidar frame
2022-06-09 lidar non rp
2022-06-22 Added battery 12V
2022-07-06 slam i rubot model
    [GoPiGo3_Wheel.stl, IR_Sensor_Sharp_GP2Y_solid.stl, Lidar.stl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]
2022-07-06 test Lidar
    [testLidar.urdf]
2022-07-13 model rubot_rp lidar min
    [rubot_rp.urdf]
2022-07-16 lidar collision
    [rubot_rp.urdf, testLidar.urdf]
2022-07-25 cad model1
    [rubot_rp2.urdf]
2022-08-31 Added models vision
    [model.sdf]
2022-09-03 meshes and rubot
    [Lidar.stl, X4.stl, lidar.stl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]
2022-09-04 rubot madel
    [Lidar.stl, X4.stl, lidar.stl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]
2022-09-28 line follow
    [model.sdf]
2022-09-29 teleop packages
    [model.sdf]
2022-09-29 teleop twist and sensor pkgs
2022-09-29 projects bringup
    [Hybrid.obj, model.sdf, sign_board.obj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]
2022-09-30 line following and teleop
    [model.sdf]
2022-10-03 line following road2
    [model.sdf]
2022-10-05 rubot rp model colision modification
    [rubot_rp.urdf]
2022-10-19 corrections in model and control md
    [rubot_rp.urdf]
2022-10-19 rubot model and figures
    [model.sdf]
2022-10-21 rubot model
    [rubot_rp.urdf]
2022-10-22 wheels turning
    [rubot_rp.urdf]
2022-10-22 model rubot mu and pid
    [rubot_rp.urdf]
2022-10-30 urdf collisions
    [rubot_rp.urdf]
2022-11-01 urdf pid
2022-11-02 inertia rubot
    [rubot.urdf, rubot0.urdf, rubot_rp.urdf]
2022-11-07 bringup line follower
    [model.sdf]
2022-11-11 model road
    [model.sdf]
2022-11-14 time correction
    [rubot_rp.urdf]
2022-11-17 plugin nexus
    [rubot_rp2.urdf]
2023-01-02 line traffic
    [X4.stl, lidar.stl, lidar0.stl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]
2023-01-03 fixed errors
    [X4.stl, lower_left_wheel.stl, lower_right_wheel.stl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]
2023-01-04 added road cross
    [model.sdf]
2023-01-04 cross world
    [model.sdf]
2023-01-10 docker update
    [Arduino (Meshed).stl, Arduino_MEGA2560.stl, Arduino_MEGA_Bumper_0003.stl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]
2023-02-07 camera topic
2023-02-21 added line follower0
    [model.sdf]
2023-03-15 Added jetson nano
2023-03-15 corrections to jetson1
2023-03-15 jetson SD card
2023-04-13 added usb and lidar corrections
2023-04-17 Installed driver wifi rock
2023-05-16 added arduino
2023-05-16 added final arduino code
    [PinMap.xlsx]
2023-06-19 corrections in model control1
    [gopigo3.urdf, gopigo3rp.urdf, nexus.urdf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]
2023-06-20 rubot control sw corrections
    [number2.stl, rubot_mpuig.urdf]
2023-06-21 added rock setup
    [Arduino (Meshed).stl, Arduino_MEGA2560.stl, Arduino_MEGA_Bumper_0003.stl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]
2023-07-04 rubot drive 2 corrections
    [rUBot_drive2.ino]
2023-07-06 codi arduino
2023-07-18 review arduino and docs
2023-07-18 model and ino
    [rubot.urdf]
2023-07-18 arduino libs
2023-07-18 arduino hardware
2023-07-20 arduino libraries
2023-09-01 encoder pin A1
2023-09-04 updated world
    [number2.stl, rubot_mpuig.urdf]
2023-09-04 updated control
    [X4.stl, mecanum_wheel_left.STL, mecanum_wheel_right.STL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]
2023-09-05 Update ws
    [Mecanum_Components.xlsx, X4.stl, mecanum_wheel_left.STL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]
2023-09-07 updated arduino folder
    [PinMap.xlsx]
2023-09-07 upload model mpuig
    [rubot_mpuig.urdf]
2023-09-07 uploaded and review control
    [rubot_mpuig.urdf]
2023-10-02 install arduino
2023-10-11 Install arduino and libs
2023-10-11 snap for arduino
2023-10-15 fix error in robot.urdf
    [rubot.urdf]
2023-11-29 arduino driver Albert
2023-11-30 added driver llorens
2023-12-14 model i bringup
    [number2.stl, rubot_mpuig.urdf]
2024-01-15 added models
    [model.sdf, sign_board.obj, sign_stand.obj]
2024-01-15 added road_base model
    [model.sdf]
2024-01-15 corrections turn left
    [model.sdf, sign_board.obj, sign_stand.obj]
2024-01-15 line follower1
    [model.sdf, rubot_mpuig.urdf]
2024-01-29 custom files
    [rubot_mpuig.urdf]
2024-01-30 sign right1
    [model.sdf, sign_board.obj, sign_stand.obj]
2024-01-30 add models
    [model.sdf]
2024-01-30 size model
    [model.sdf]
2024-01-31 sign left
    [model.sdf, sign_board.obj, sign_stand.obj]
2024-01-31 world project
    [model.sdf, sign_board.obj, sign_stand.obj]
2024-02-07 print diff
2024-02-09 bringup files deleted
    [rubot_mpuig.urdf]
2024-02-12 video inserted
2024-02-12 video inserted 2
2024-02-18 update arduino and bugs
2024-02-20 updated arduino program
2024-02-21 changes for raspberrypi4
2024-02-26 arduino i params slam
2024-02-27 pid control
2024-03-04 lidar corrections
2024-03-18 corrections in wall follower and IMU
2024-04-08 wall follower pid
    [rubot_mpuig.urdf]
2024-05-04 arduino drive
2024-06-06 rubot driver
2024-06-06 driver pi
2024-06-10 lidar control
2024-06-12 driver final
2024-07-08 first driver
2024-07-16 raspberry bringup update
2024-07-23 new driver
2024-07-23 updated control and driver
2024-07-24 driver OL
2024-07-26 install arduino and joy
2024-07-26 bringup pi and arduino
2024-10-16 models and rubot
    [X4.stl, number0.stl, number1.stl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]
2024-10-18 updated bringup
    [rubot.urdf, rubot_custom.urdf]
2024-10-26 lidar custom2
2024-11-10 bringup sw and number2
    [number2.stl]
2024-11-10 updated lidar test
2024-12-14 amcl for lidar priority
2024-12-16 limo model
    [empty.urdf, limo_ackerman.xacro, limo_collision.stl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]
2024-12-31 updated driver
    [Arduino (Meshed).stl, Arduino_MEGA2560.stl, Arduino_MEGA_Bumper_0003.stl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]
2025-01-11 raspberry install
2025-02-05 slam lidar
2025-02-18 updated urdf
    [GoPiGo3_Wheel.stl, IR_Sensor_Sharp_GP2Y_solid.stl, X4.stl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]
2025-02-18 piCamera correction
    [rubot.urdf]
